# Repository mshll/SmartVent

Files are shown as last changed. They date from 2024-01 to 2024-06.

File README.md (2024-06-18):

# LaunchPilot: Smart Vent

Senior Capstone Project (Spring 2024)

Industry Sponsor: Cedrec Sumimoto

Faculty Advisor: Andrew Greenberg

Team members: Meshal Almutairi, Michael Fontaine, Abdulaziz Alateeqi,
Fawzan Alfahad, John Michael Mertz

## Overview

We teamed up with Launch Pilot to make a smart vent system. The main goal was to ensure safe indoor air quality by monitoring CO2 levels. When the CO2 level goes above the safe threshold, the system automatically activates to circulate fresh clean air into the room, thus reducing the CO2 level.

## Approach

We designed the system using sensors to detect CO2 levels, temperature, and
humidity. The design also includes fans that operate at different speeds to help with fresh air circulations, an LCD to display the sensor readings, and a microcontroller as the brain of this project. We also implemented a web-based dashboard that is accessible via a local network for remote monitoring and adjustments such as changing the CO2 level threshold, turning the system entirely on or off, and controlling the fan's speed. Additionally, we integrated buttons on the fans to provide direct control for the different settings.

## Results

Our system successfully reads carbon dioxide levels and activates the fans accordingly. Moreover, the web-based dashboard and the buttons work great when adjusting different settings. The LCD provides real-time readings from the sensors as well as any warnings. Users can control the system directly or remotely, which has been a major plus.

## Completed Build
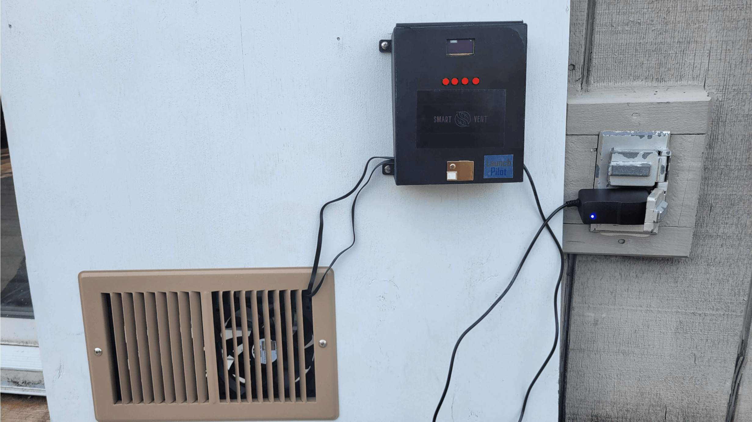
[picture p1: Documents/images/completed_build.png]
completed_smart vent


## Dashboard Preview
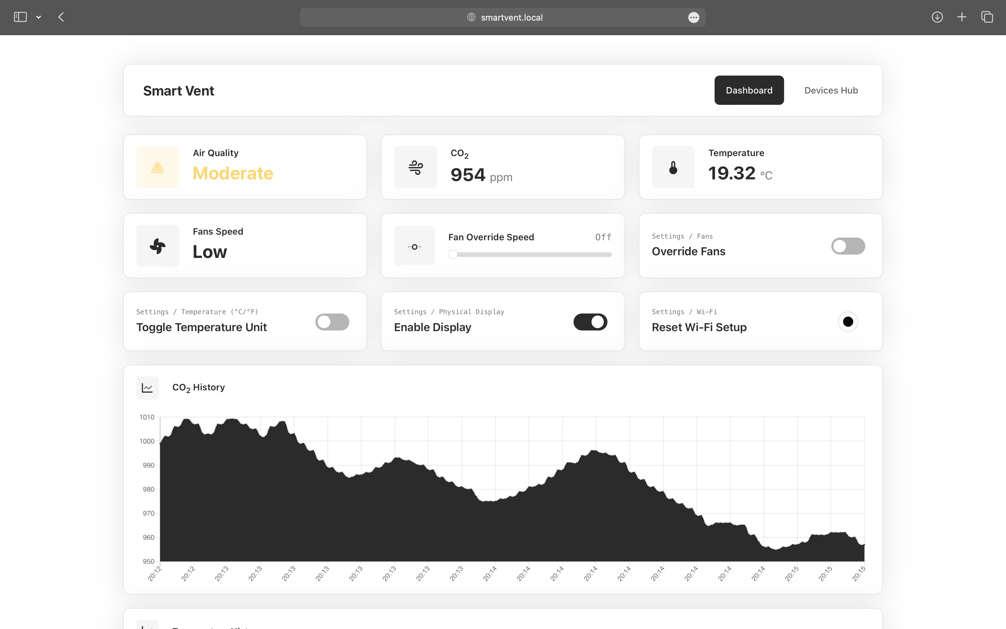
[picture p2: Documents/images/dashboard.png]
dashboard


## Device OLED Display Preview
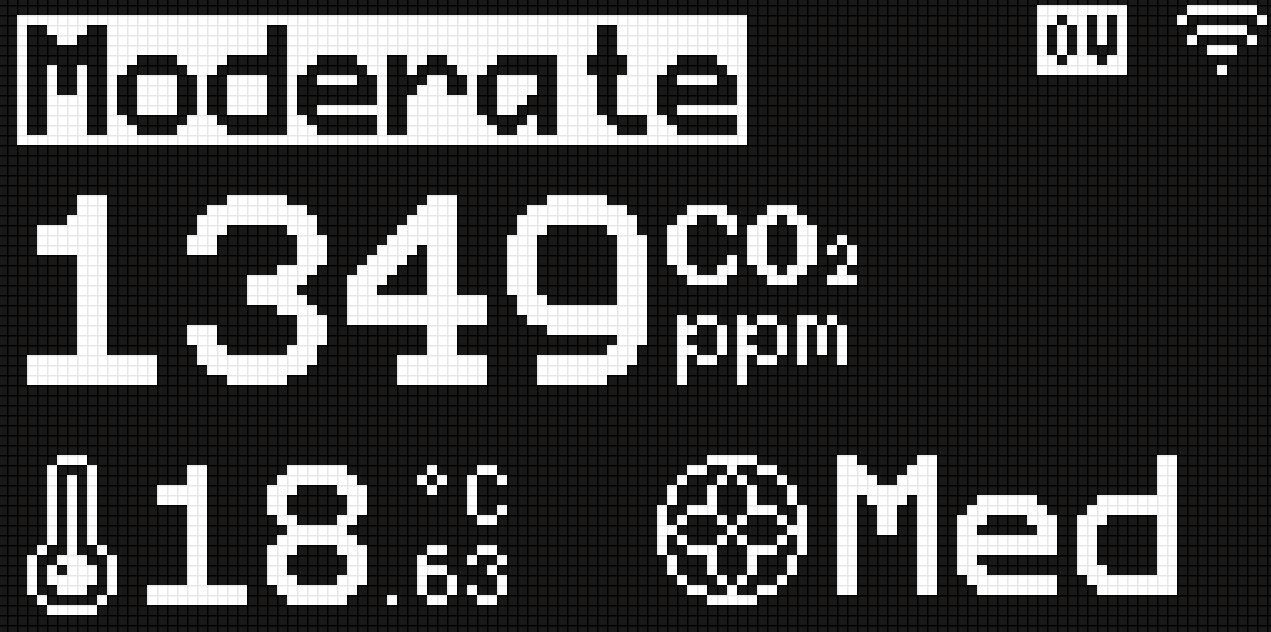
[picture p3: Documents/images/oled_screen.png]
oled


## Project Report

For more details on the project, please refer to the [Project Report](Documents/Smart_Vent_Report.pdf)

## User Manual

For instructions on how to use the system, please refer to the [User Manual](Documents/Smart_Vent_User_Manual.pdf)

## License

This project is licensed under the AGPL-3.0 License - see the [LICENSE](LICENSE) file for details.

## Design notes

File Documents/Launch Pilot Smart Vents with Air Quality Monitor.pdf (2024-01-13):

# Smart Vents with Air Quality Monitor

Background
Prolonged exposure to poor quality air can lead to respiratory problems, heart disease, and cognitive decline. This is a major issue that plagues dungeon dwelling engineers and creators across the world.

Objective
Design an air vent unit capable of monitoring ambient air quality and automatically (de)activating its fans to optimize airflow. The unit should dimensionally fit standard air vents.

System Requirements
- Air Quality Sensor
- Simple Display Screen
- Buttons for Toggling Settings
- Dual 120mm Fan System
- Battery Powered
- Micro USB Charging Port
- Smart Home Wi-Fi Connectivity (optional)

Timeline

### 1. Finalize Proposal 2. Component Selection and Acquisition 3. Validation on Evaluation Board 4. Design and Assemble PCBA 5. Prototype and Testing 6. Finalize and Complete Deliverables

Deliverables
- Schematic(s) with bill of materials
- Mechanical drawings and CAD models (if any)
- System test report
- Working prototypes (both the development board and the custom PCBA)
- Any and all supporting documents, software, hardware, etc.

Note: Meetings will be conducted via Discord or some other similar platform. Project Manager is located in Southern California but will visit the team as necessary for the progress of the project.

Existing similar product for reference

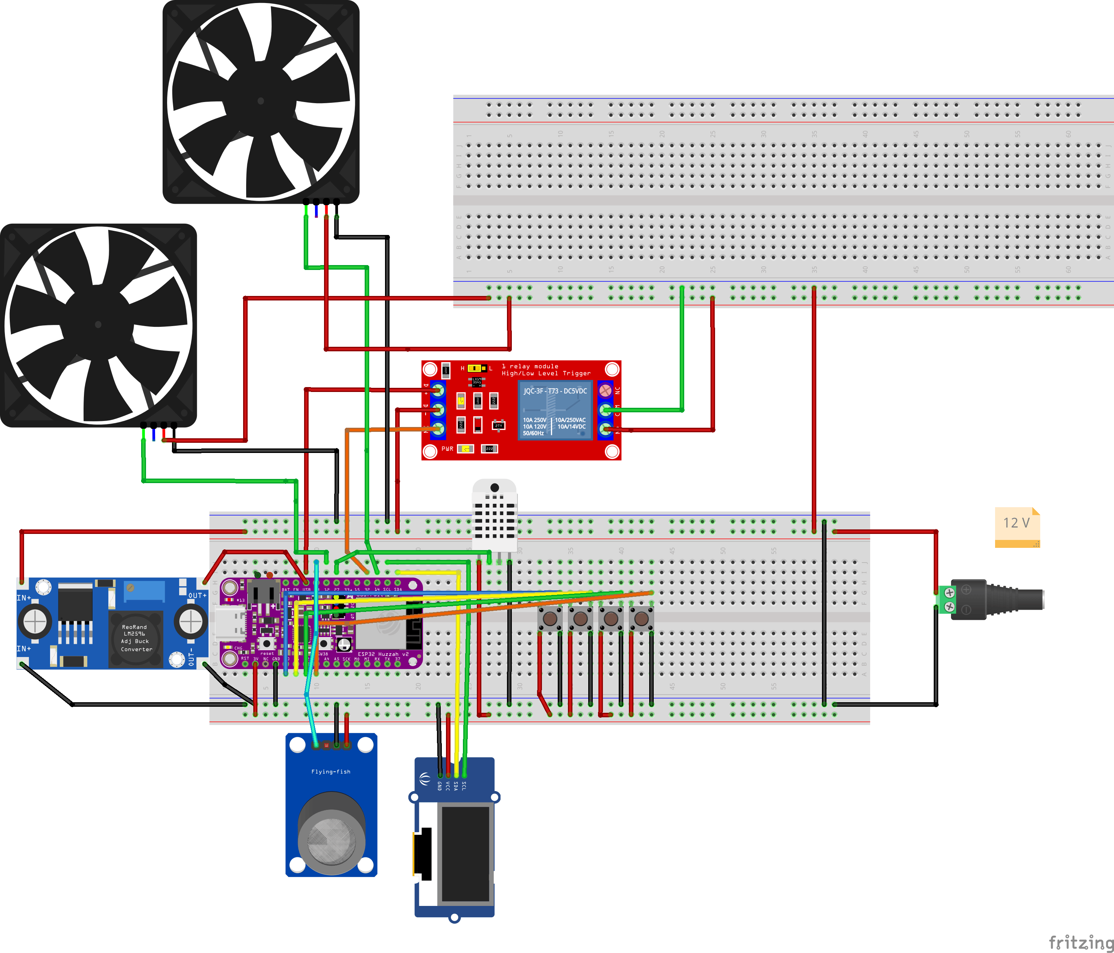
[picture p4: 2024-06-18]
Documents/images/prototype schematic_bb.png

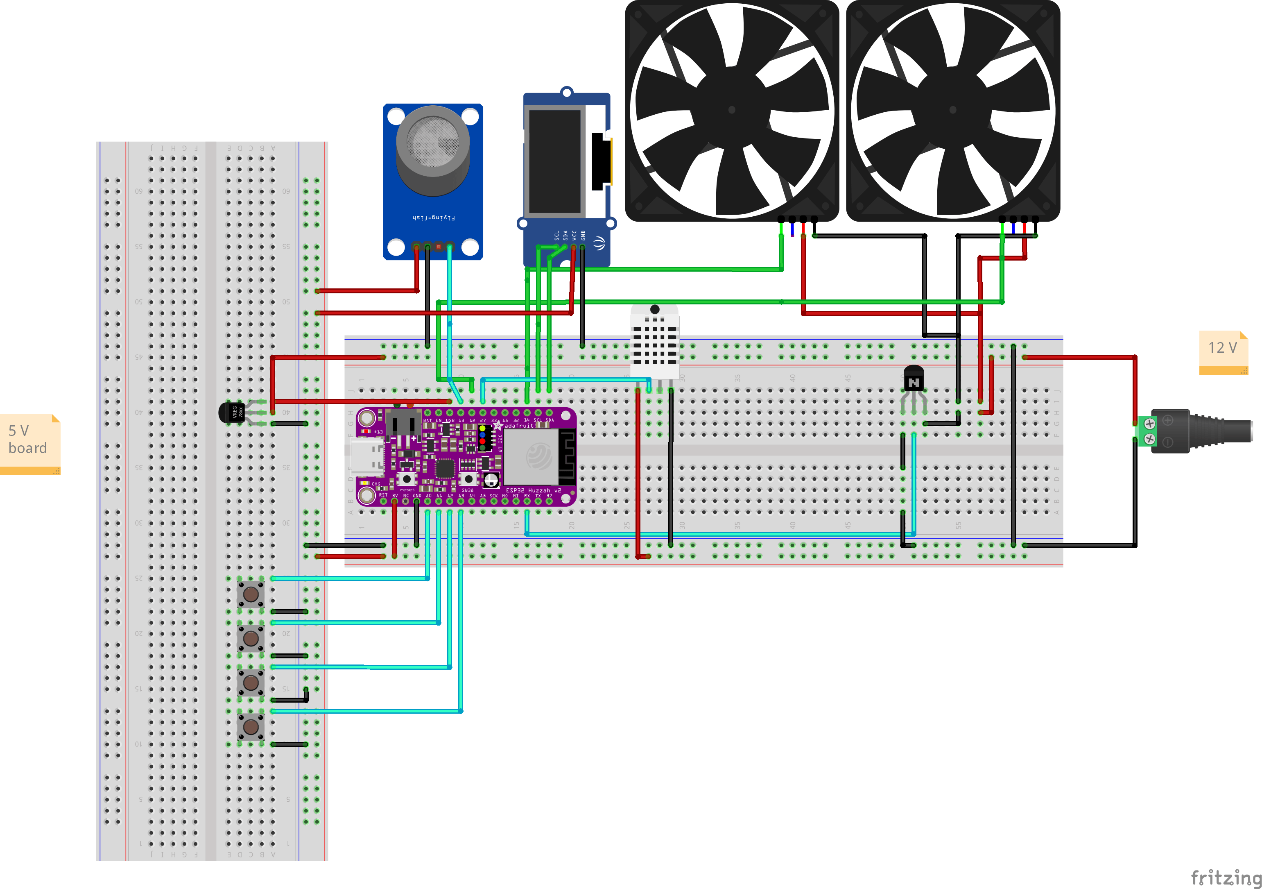
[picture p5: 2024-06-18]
Documents/images/Layout final.png

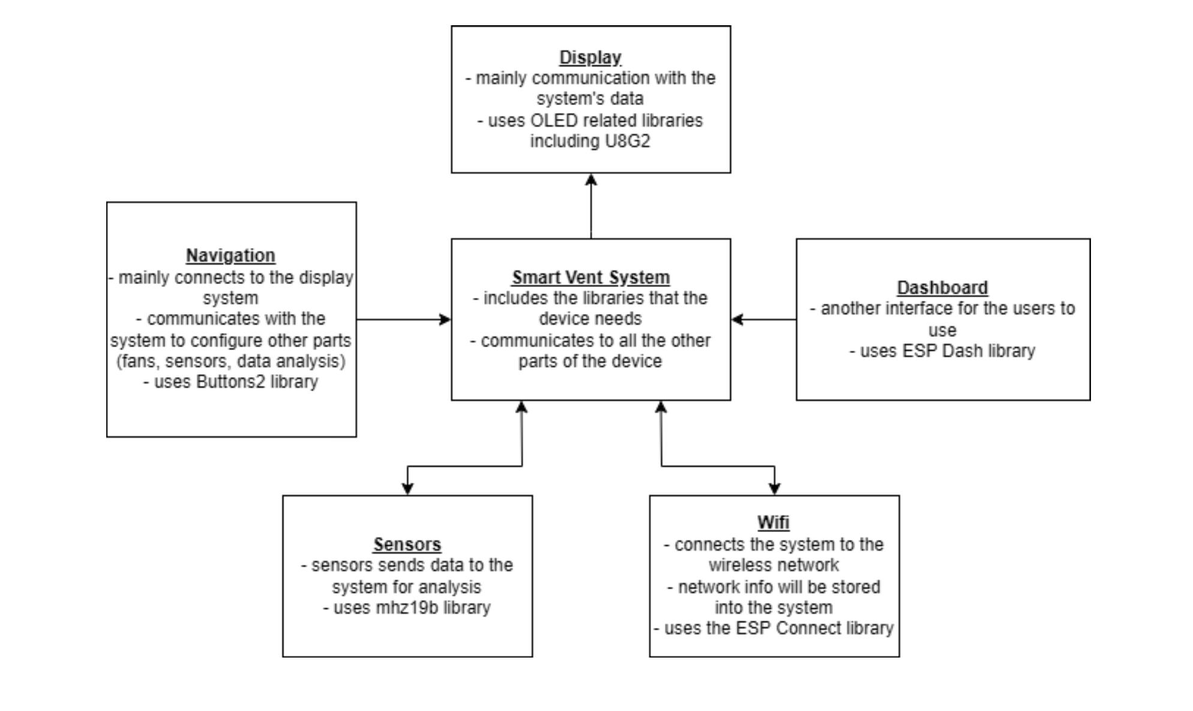
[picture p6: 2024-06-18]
Documents/images/system_diagram.png

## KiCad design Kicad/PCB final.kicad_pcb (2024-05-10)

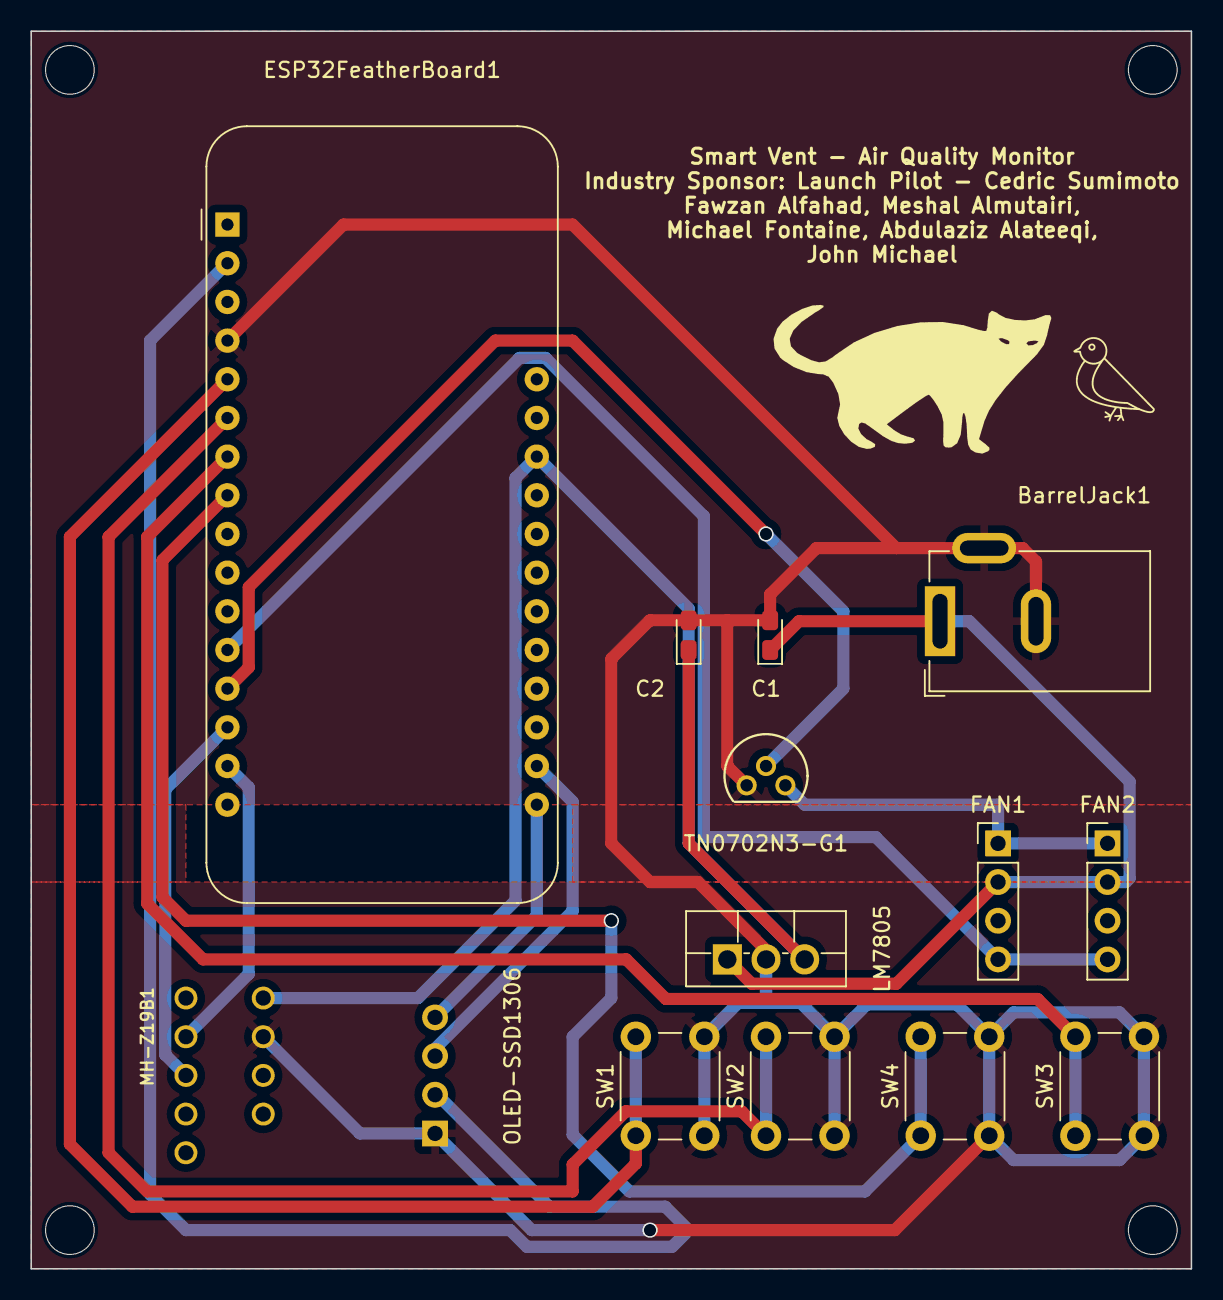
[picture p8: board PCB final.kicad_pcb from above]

Board: 2 copper layers, 76.2 x 81.3 mm, 14 parts (0 on the bottom side), 15 nets.

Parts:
BarrelJack1: BarrelJack_GCT_DCJ200-10-A_Horizontal
C1: 0.1pF; CP_EIA-2012-12_Kemet-R_Pad1.30x1.05mm_HandSolder
C2: 0.47pF; CP_EIA-2012-12_Kemet-R_Pad1.30x1.05mm_HandSolder
ESP32FeatherBoard1: Adafruit_Feather
FAN1, FAN2: PinHeader_1x04_P2.54mm_Vertical
LM7805: TO-220F-3_Vertical
MH-Z19B1: MH-Z19B-FOOT
OLED-SSD1306: Adafruit_SSD1306
SW1, SW2, SW3, SW4: SW_PUSH_6mm_H4.3mm
TN0702N3-G1: TO-92_MC_MCH

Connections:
FAN1 (GND): FAN1.1, FAN2.1, TN0702N3-G1.3 (DRAIN)
FAN (PWM): ESP32FeatherBoard1.12 (MOSI/IO18), FAN1.4, FAN2.4
GND: BarrelJack1.2, BarrelJack1.3, C1.2, C2.2, ESP32FeatherBoard1.4 (GND), LM7805.2 (GND), MH-Z19B1.GND, OLED-SSD1306.1 (GND), SW1.2, SW2.2, SW3.2, SW4.2, TN0702N3-G1.1 (SOURCE)
unnamed: ESP32FeatherBoard1.2 (3V3), OLED-SSD1306.2 (VCC)
unnamed: ESP32FeatherBoard1.6 (DAC1/A1), SW2.1
unnamed: ESP32FeatherBoard1.5 (DAC2/A0), SW1.1
unnamed: ESP32FeatherBoard1.7 (I34/A2), SW3.1
unnamed: ESP32FeatherBoard1.8 (I39/A3), SW4.1
unnamed: ESP32FeatherBoard1.13 (MISO/IO19), TN0702N3-G1.2 (GATE)
unnamed: ESP32FeatherBoard1.14 (RX/IO16), MH-Z19B1.TX
unnamed: ESP32FeatherBoard1.18 (SCL/IO22), OLED-SSD1306.3 (SCL)
unnamed: ESP32FeatherBoard1.17 (SDA/IO23), OLED-SSD1306.4 (SDA)
unnamed: ESP32FeatherBoard1.15 (TX/IO17), MH-Z19B1.RX
unnamed: BarrelJack1.1, C2.1, FAN1.2, FAN2.2, LM7805.1 (IN)
USB: C1.1, ESP32FeatherBoard1.26 (USB), LM7805.3 (OUT), MH-Z19B1.VIN

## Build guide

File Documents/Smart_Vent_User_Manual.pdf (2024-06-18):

# Smart Vent User Manual

# Launch Pilot

Appendix I: Smart Vent User Manual - Launch Pilot

User Manual Table of Contents

Product Introduction

The Smart Vent is designed to monitor and improve air quality in its surroundings. It

features a sensor that detects carbon dioxide levels and temperature. When carbon

dioxide levels exceed the set limits, the Smart Vent's fans will activate.

Device Overview

- Sensor: Measures the CO2 levels and ambient temperature in the surrounding

area.

- Display Screen: Displays the CO2, temperature,
- Buttons: Navigate through the display options.
- Built-in Wi-Fi: Provides access to remote dashboard
- Power plug: Connects to the device barrel jack.

Quick Start

I. Mount the Device: Attach the Smart Vent device to the wall near your vent or duct.

II. Power the Device: Plug the power adapter into an electrical outlet.

III. Initial Display: The display screen will light up, showing the main interface.

IV. Stabilization Period: Allow the device one to two minutes to stabilize.

V. Reading Display: When the readings begin to appear, your device is correctly set

up.

Built-in Display

1. Air quality threshold indicator. The following are the threshold levels:
a. Good: below 800 ppm.
b. Moderate: 800 to 1400 ppm.
c. Poor: 1400 to 2000 ppm.
d. Unhealthy: 2000 to 3000 ppm.
e. Hazardous: above 3000 ppm.
2. CO2 concentration level in ppm (parts per million).
3. Temperature of the air in Celsius or Fahrenheit.
4. Current speed of the fans (Off, Low, Med, High, Max).
5. Wi-Fi connection indicator.
6. Fans override indicator

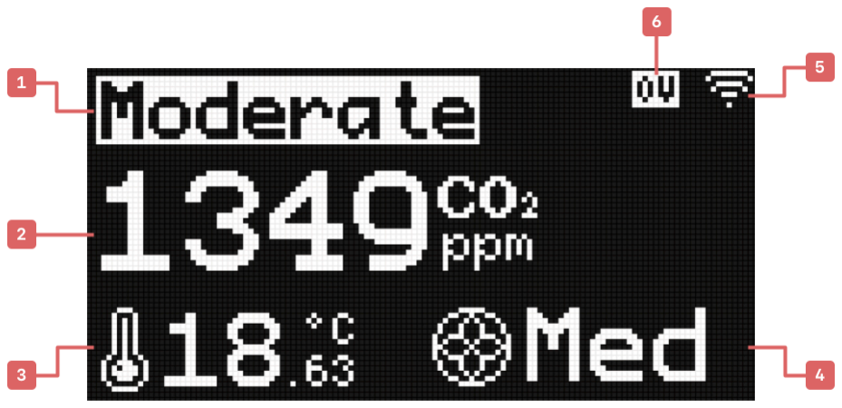
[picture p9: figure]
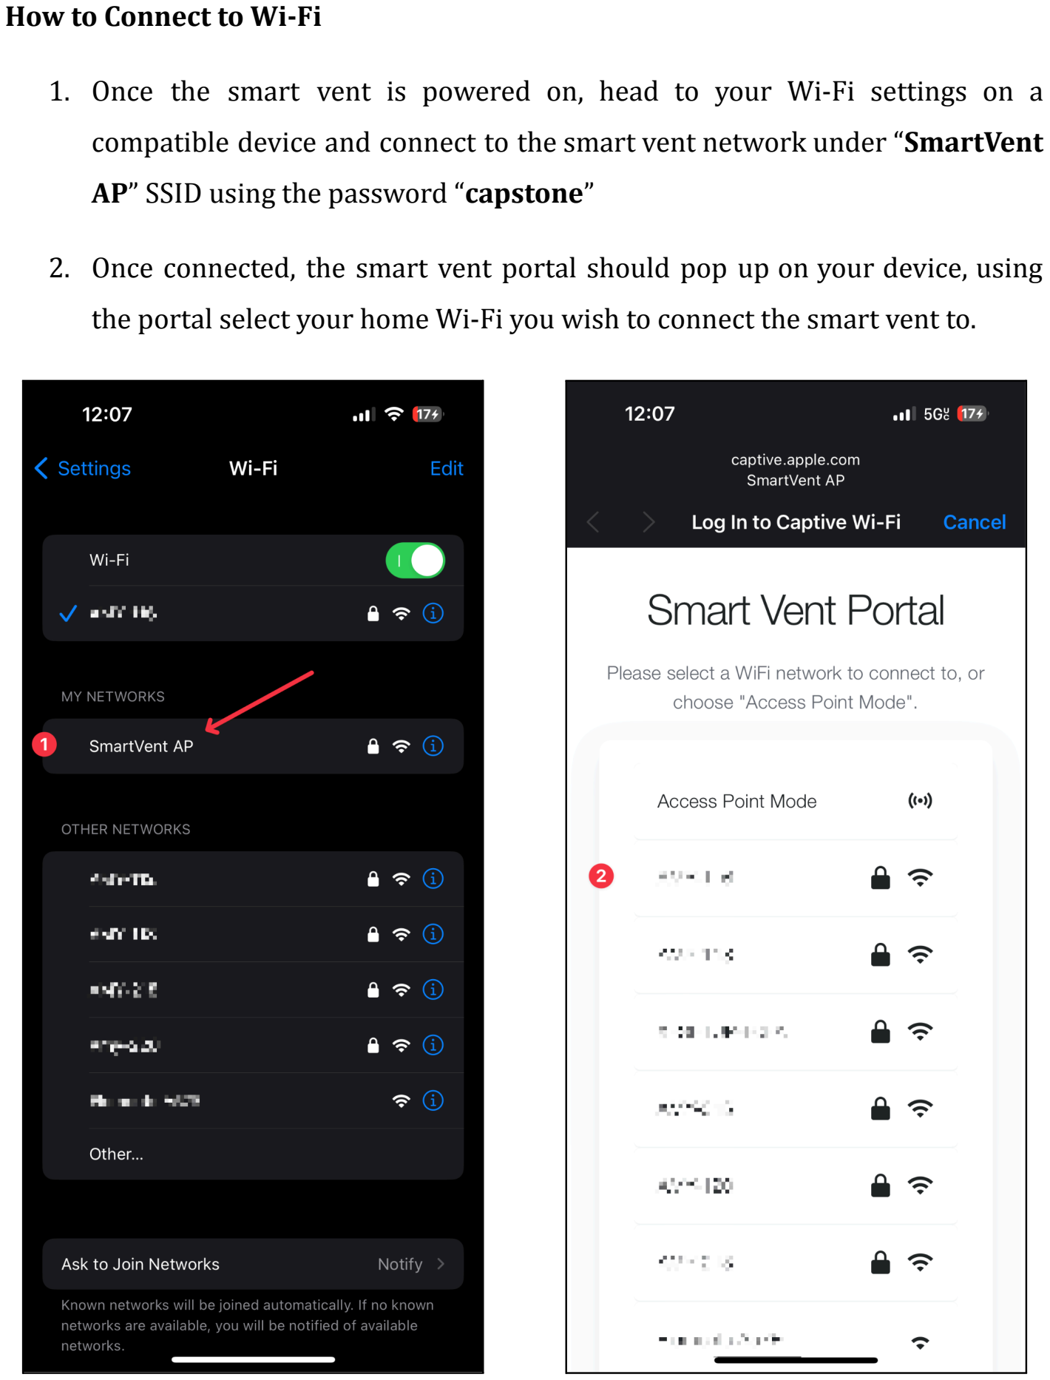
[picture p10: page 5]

How to Connect to Wi-Fi

1. Once the smart vent is powered on, head to your Wi-Fi settings on a

compatible device and connect to the smart vent network under “SmartVent

AP” SSID using the password “capstone”

2. Once connected, the smart vent portal should pop up on your device, using

the portal select your home Wi-Fi you wish to connect the smart vent to.

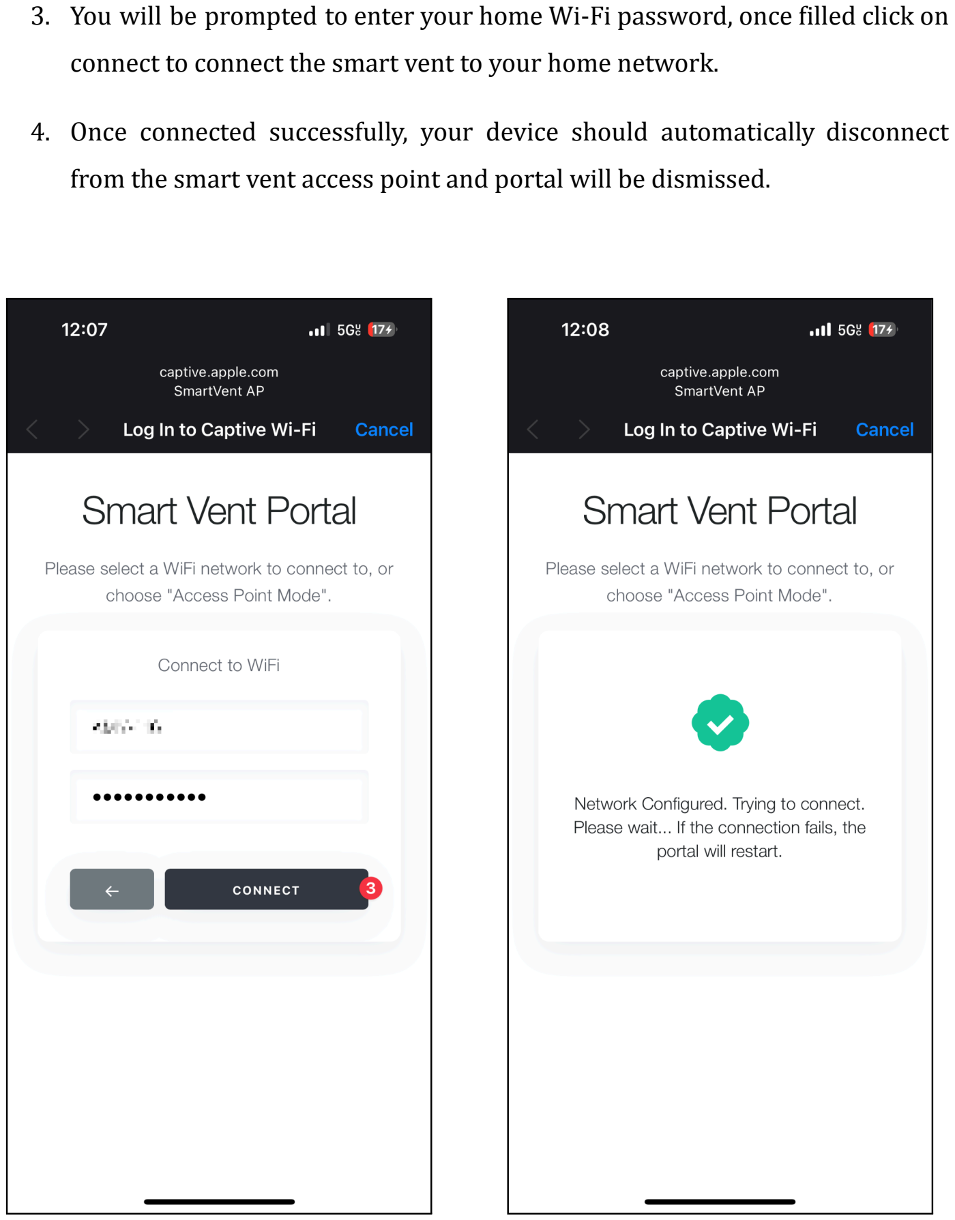
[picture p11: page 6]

3. You will be prompted to enter your home Wi-Fi password, once filled click on

connect to connect the smart vent to your home network.

4. Once connected successfully, your device should automatically disconnect

from the smart vent access point and portal will be dismissed.

5. Then connect your device to your home Wi-Fi and enter the web address

‘smartvent.local’ in your browser to access the remote dashboard.

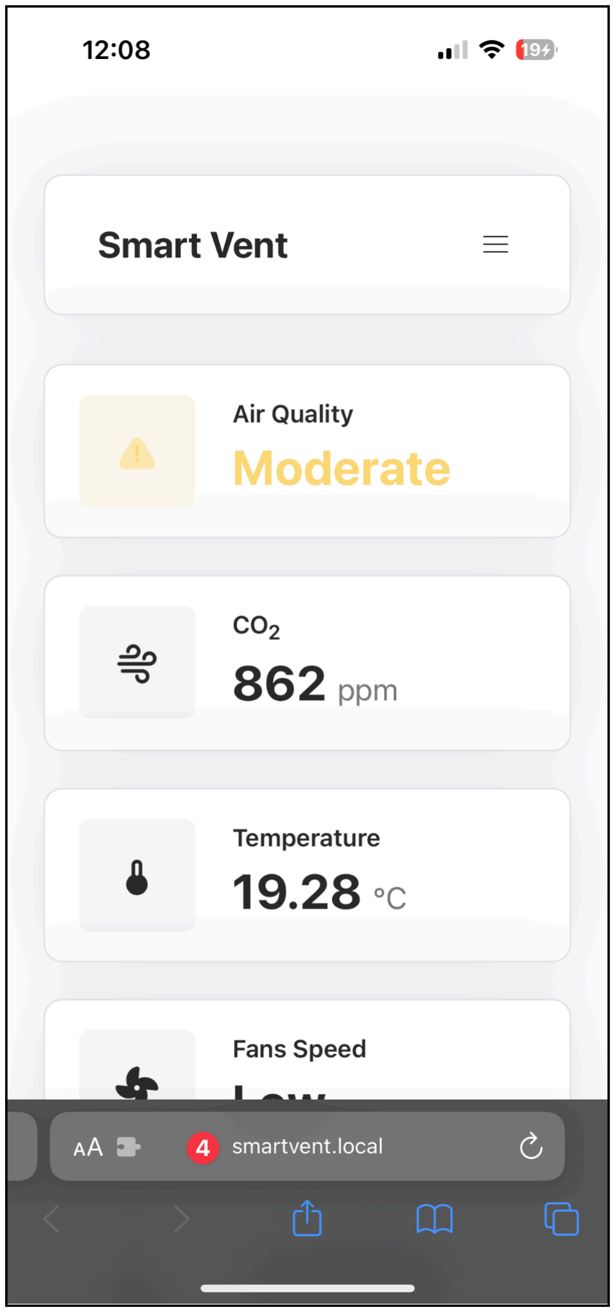
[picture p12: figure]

Wi-Fi Remote Dashboard

The smart vent dashboard can be accessed using ‘smartvent.local’ web address on

your browser if your device is connected to the same Wi-Fi network as the smart

vent. The dashboard offers a remote overview of the smart vent and displays the

same readings as the display on the smart vent.

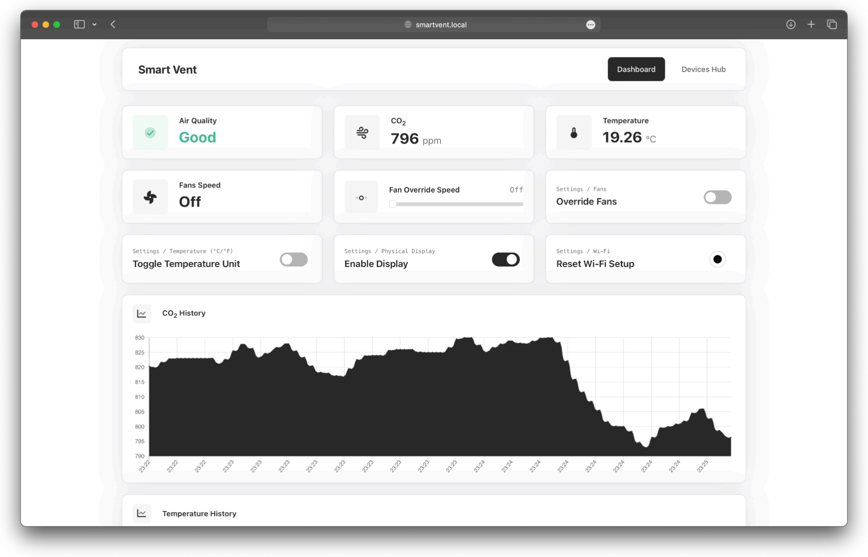
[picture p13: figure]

Technical Specifications

- Power Input: 12V - 1A via barrel jack
- Connectivity: Wi-Fi (2.4GHz)
- Nondispersive infrared (NDIR) sensor to measure CO2 concentration
- CO2 Sensor Range: 400-5000 ppm
- Temperature Range: 0°C to 50°C (32°F to 122°F)

Safety Information

- Indoor Use Only: The Smart Vent is designed for indoor use only.
- Avoid Moisture: Do not expose the device to water or moisture.
- Avoid Extreme Temperatures: Do not put the device in an extremely hot or

cold environment (0°C to 50°C).
- Power Safety: Use only the provided power adapter (DC 12V - 1A).

Customer Support

- Email: support@smartvent.com
- Phone: +1 (800) 123-4567
- Website: www.smartvent.com/support

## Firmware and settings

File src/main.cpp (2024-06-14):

/**
 *    _____                      __     _    __           __
 *   / ___/____ ___  ____ ______/ /_   | |  / /__  ____  / /_
 *   \__ \/ __ `__ \/ __ `/ ___/ __/   | | / / _ \/ __ \/ __/
 *  ___/ / / / / / / /_/ / /  / /_     | |/ /  __/ / / / /_
 * /____/_/ /_/ /_/\__,_/_/   \__/     |___/\___/_/ /_/\__/
 *
 * @file    main.cpp
 * @author  Team 8:
 *            Abdulaziz Alateeqi,
 *            Meshal Almutairi,
 *            Fawzan Alfahad,
 *            Michael Fontaine,
 *            John Michael Mertz.
 * @brief   Smart Vent capstone project source code.
 * @copyright Copyright (c) 2024
 *
 */

#include "buttons.h"
#include "common.h"
#include "dashboard.h"
#include "fans.h"
#include "mhz19b.h"
#include "oled.h"
#include "preferences_manager.h"
#include "webserver.h"

/* global variables */
extern AsyncWebServer server;  // defined in dashboard.cpp
WebServer webserver(&server);
Dashboard dashboard;
MHZ19B mhz19b;
OLED oled;
Fans fans;
Buttons buttons;
PreferencesManager pref_manager("smartvent");

void core1_task(void* parameter);

void setup() {
  Serial.begin(9600);
  pref_manager.init();
  oled.init();
  webserver.init();
  mhz19b.init();
  fans.init();
  dashboard.init();
  buttons.init();
  xTaskCreatePinnedToCore(core1_task, "core1_task", 10000, NULL, 1, NULL, 1);
}

void loop() {
  webserver.loop();
  mhz19b.loop();
  dashboard.loop();
  fans.update(mhz19b.get_co2());
}

void core1_task(void* parameter) {
  for (;;) {
    // Run buttons task on core 1 to avoid conflicts with other tasks
    oled.loop();
    buttons.loop();
    vTaskDelay(10);
  }
}

/**
 * @brief Decrement a value with wrap-around.
 */
int decrement(int val, int size) {
  return (val + size - 1) % size;
}

/**
 * @brief Increment a value with wrap-around.
 */
int increment(int val, int size) {
  return (val + 1) % size;
}

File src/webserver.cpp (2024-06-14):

/**
 * @file  webserver.cpp
 * @copyright Copyright (c) 2024
 */

#include "webserver.h"
#include "common.h"
#include "wifiFix.h"

#define HEARTBEAT_INTERVAL 5000      /*ms*/
#define CHECK_DEVICES_INTERVAL 16000 /*ms*/

WiFiClient* wifi = new WiFiClientFixed();

/**
 * @brief Constructor for the WebServer class.
 * @param server The AsyncWebServer object.
 */
WebServer::WebServer(AsyncWebServer* server) {
  _server = server;
  is_connected = false;
  device_id = String((uint32_t)ESP.getEfuseMac(), HEX);
  device_name = DEVICE_NAME;
  leader_id = "";
  is_leader = false;
  multicast_ip = IPAddress(233, 255, 255, 255);
  udp_port = 4096;
  hostname = String(HOSTNAME) + "-" + device_id;
  heartbeat_timeout = 15000;
  last_log = 0;

  heartbeat_ticker = new TickTwo(std::bind(&WebServer::send_heartbeat, this), HEARTBEAT_INTERVAL);
  check_devices_ticker = new TickTwo(std::bind(&WebServer::check_devices, this), CHECK_DEVICES_INTERVAL);
}

/**
 * @brief Destructor for the WebServer class.
 */
WebServer::~WebServer() {
  delete heartbeat_ticker;
  delete check_devices_ticker;
}

void WebServer::init() {
  // clear configuration
  _server->on("/clear", HTTP_GET, [&](AsyncWebServerRequest* request) {
    Serial.println("Clearing configuration...");
    reset_wifi();
    request->send(200);
  });

  // add a rewrite which is only applicable in AP mode and STA mode, but not in Captive Portal mode
  _server->rewrite("/", "/dash").setFilter([](AsyncWebServerRequest* request) { return ESPConnect.getState() != ESPConnectState::PORTAL_STARTED; });

  if (get_device_index(device_id) == -1) devices.push_back({device_id, WiFi.localIP(), millis()});

  // network state listener for async mode
  ESPConnect.listen([&](ESPConnectState previous, ESPConnectState state) {
    JsonDocument doc;
    ESPConnect.toJson(doc.to<JsonObject>());
    serializeJsonPretty(doc, Serial);
    Serial.println();

    is_connected = false;

    switch (state) {
      case ESPConnectState::NETWORK_CONNECTED:
      case ESPConnectState::AP_STARTED:
        //*************************************************************
        udp.beginMulticast(multicast_ip, udp_port);
        is_connected = true;

        Serial.println("==========> NETWORK CONNECTED");
        send_election_message();
        determine_leader();
        setup_mdns();

        heartbeat_ticker->start();
        check_devices_ticker->start();
        setup_time();

        _server->begin();
        break;
        //*************************************************************
      case ESPConnectState::NETWORK_DISCONNECTED:
        _server->end();
      default:
        break;
    }
  });

  ESPConnect.setAutoRestart(false);
  ESPConnect.setBlocking(false);
  ESPConnect.setCaptivePortalTimeout(86400);
  ESPConnect.setConnectTimeout(10);

  Serial.println("====> Trying to connect to saved WiFi or will start portal in the background...");
  ESPConnect.begin(_server, HOSTNAME, AP_SSID, AP_PASS);
}

/**
 * @brief Main loop for the web server.
 */
void WebServer::loop() {
  ESPConnect.loop();

  if (millis() - last_log > 5000) {
    Serial.println("IP: " + WiFi.localIP().toString());
    Serial.println("MAC: " + WiFi.macAddress());
    Serial.println("ID: " + device_id + " // " + "Leader: " + leader_id + " // " + "URL: http://" + get_hostname() + ".local");
    last_log = millis();
  }

  if (!is_connected) return;

  handle_incoming_packets();
  heartbeat_ticker->update();
  check_devices_ticker->update();
}

/**
 * @brief Sets up mDNS responder using the appropriate hostname depending on the device's role.
 */
void WebServer::setup_mdns() {
  delay(500);
  if (MDNS.begin(get_hostname().c_str())) {
    MDNS.addService("http", "tcp", 80);
    Serial.println("mDNS responder started on " + get_hostname());
  } else {
    Serial.println("Error setting up MDNS responder!");
  }
}

/**
 * @brief Sends a heartbeat message to all devices in the network to indicate that the device is still active.
 */
void WebServer::send_heartbeat() {
  int device_index = get_device_index(device_id);
  String message = "HB:" + device_id + ":" + (is_leader ? "1" : "0");
  Serial.println("---> Sending heartbeat message: " + message);
  udp.beginMulticastPacket();
  udp.write((const uint8_t*)message.c_str(), message.length());
  udp.endPacket();
  devices.at(device_index).last_heartbeat = millis();
}

/**
 * @brief Sends an election message to all devices in the network to initiate an election for the leader.
 */
void WebServer::send_election_message() {
  String message = "ELECT:" + device_id;
  Serial.println("---> Sending election message: " + message);
  udp.beginMulticastPacket();
  udp.write((const uint8_t*)message.c_str(), message.length());
  udp.endPacket();
}

/**
 * @brief Handles incoming packets from the network.
 */
void WebServer::handle_incoming_packets() {
  int packetSize = udp.parsePacket();
  if (packetSize) {  // If a packet is available
    char packet[255];
    int len = udp.read(packet, 255);
    if (len > 0) {
      packet[len] = 0;
    }
    String message = String(packet);
    Serial.println("Received packet: " + message);

    // Parse the message
    int sepertor = message.indexOf(':');
    int second_sepertor = message.indexOf(':', sepertor + 1);
    String msg_type = message.substring(0, sepertor);
    String sender_id = message.substring(sepertor + 1, second_sepertor);

    if (msg_type == "HB") {  // If the message is a heartbeat message, update the device's last heartbeat
      bool leader = message.substring(second_sepertor + 1) == "1";
      update_device(sender_id, leader);

    } else if (msg_type == "ELECT") {  // If the message is an election message, initiate an election for the leader
      if (device_id < sender_id) {
        send_election_message();
      }
      update_device(sender_id, false);
      // determine_leader();
    }
  }
}

/**
 * @brief Updates the device's information in the devices vector.
 * @param id The device's ID.
 * @param leader Whether the device is the leader or not.
 */
void WebServer::update_device(String id, bool leader) {
  bool found = false;
  for (auto& device : devices) {
    if (device.id == id) {
      device.last_heartbeat = millis();
      found = true;
      break;
    }
  }
  if (!found) {
    DeviceInfo new_device;
    new_device.id = id;
    new_device.ip = udp.remoteIP();
    new_device.last_heartbeat = millis();
    devices.push_back(new_device);
    Serial.println("New device found: " + id);
  }

  if (leader || !found) {  // If the sender is the leader or the device is new
    determine_leader();
  }
}
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

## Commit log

2024-01-29 esp32 pinouts added
2024-02-05 update MQ135 calibration
2024-02-25 add air and push button cards to dashboard
2024-02-25 basicFour_Buttons.ino is for the four buttons
    This is a basic test for the four buttons. This requires four pins for reading.
2024-03-01 added relay stuff to completely turn fans off
2024-03-01 initial fan integration, still TODO also add simple oled toggle
2024-03-02 prototype layout
    [prototype schematic.fzz]
2024-03-02 added Buttons2 library
2024-03-02 made the code use Button2 library
2024-03-17 added button2 library to it and uncommented delays
2024-03-20 added idle timer interrupt narrowed button press type needs
2024-04-25 added sleep button
2024-04-26 added Display to Fan Speed
2024-04-27 initial multi-device support implemented udp to broadcast and receieve mac addresses from other devices on the same network and elect host board
2024-04-30 fix multi-device support
2024-05-02 update dashboard for multi-device support
2024-05-02 update webserver to serialize devices for dashboard
2024-05-05 update dashboard - add vent info to stats - show device name + active devices count - change fan card - add air quality
2024-05-05 implement automatic time setup, change esp32 partition scheme using ntp server and worldtimeapi.org for time setup
    [huge_app.csv]
2024-05-05 update pins for 1st iteration build, fix bugs, add fan override option
    [webserver.cpp]
2024-05-05 use new mh-z19b sensor
2024-05-06 remove old sensors code & dependencies
2024-05-09 Add Kicad files
    [PCB final-B_Cu.gbr, PCB final-B_Mask.gbr, PCB final-B_Paste.gbr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]
2024-05-10 Add Kicad files (Updated)
    [PCB final-B_Cu.gbr, PCB final-B_Mask.gbr, PCB final-B_Paste.gbr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]
2024-05-10 move Kicad drill files
    [PCB final-NPTH.drl, PCB final-PTH.drl]
2024-05-19 bug fix, change co2 thresholds
    [common.h, fans.cpp, main.cpp]
2024-06-01 update UI, fix fans bug
    [buttons.cpp, common.h, fans.cpp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]
2024-06-07 finished buttons for changing Termperature Unit
2024-06-07 added Fan Override Control
2024-06-07 added a simple Wifi Reset option
    [buttons.cpp]
2024-06-09 flipped increment and decrement for Fan Speed Override, added to display IP Address when connected to wifi, failed to add MAC Address
    [buttons.cpp]
2024-06-14 implement preferences manager to make options persistent, finish wifi info screen, bug fixes
    [buttons.cpp, common.h, fans.cpp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]
